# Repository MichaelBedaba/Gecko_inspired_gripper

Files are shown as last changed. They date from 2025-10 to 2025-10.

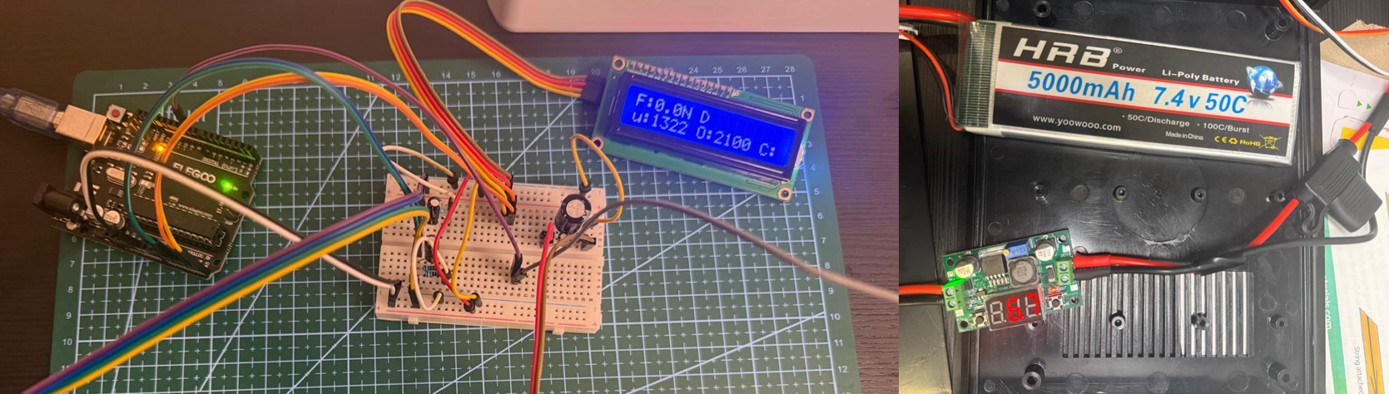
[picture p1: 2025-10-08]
Control Cicuit/setup.png

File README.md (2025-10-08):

# Development and Experimental Evaluation of Gecko-Inspired Robotic Gripper

## Code Procedures
1) **Force_Sensors_Calibration** → To calibrate FSRs with known weights; update M/B in code.
2) **Setting_Servo_Limits** → To set safe OPEN/CLOSE pulses (e.g., 2100/1500 μs) and save to EEPROM.
3) **Gripper_Operation_Testing** → To run integrated test: grip, read forces, show on LCD, log results.

## Required Libraries
- LiquidCrystal_I2C, Wire, EEPROM

## Wiring (Arduino Uno)
- Servo PWM → D9 (servo power from external 6 V, common GND)
- FSR Left → A0 (voltage divider 4.7k-ohm)
- FSR Right → A1 (voltage divider 4.7k-ohm)
- LCD SDA → A4, LCD SCL → A5

## Procedure

 **Power On:**
     -	Servo remains detached (no movement on startup).
     -	Arduino loads previous calibration and servo limit values from EEPROM.
 **Load Configuration:**
     -	Retrieve FSR calibration constants (M, B) and servo endpoint limits (OPEN/CLOSE µs).
 **Sensor Reading:**
     -	Continuously read force from Left (A0) and Right (A1) FSRs.
     -	Convert analog readings to Force (N) using calibration data.
     -	If total force exceeds predefined maximum → block servo closing.
 **Servo Activation (ARM):**
     -	Attach servo to enable motion.
     -	Manually adjust servo pulse width to control jaw opening/clamping.
     -	LCD displays real-time values:
             o	Total Force (N)
             o	Current servo pulse (µs)
             o	System status (ARM / DISARM)
 **Data Recording:**
     -	Record readings for each test object and jaw type.
     -	Include parameters such as object ID, pulse (µs), forces (N), slip, and surface marks.
 **Iteration:**
     -	Replace current jaw type (Gecko / Soft / Hard).
     -	Repeat measurement and recording for each configuration.
     -	Compare performance results across jaw types.

## By:
     Michael George - M00979224
     Supervisor: Dr. Judhi Prasetyo
     MSc Robotics, Middlesex University Dubai

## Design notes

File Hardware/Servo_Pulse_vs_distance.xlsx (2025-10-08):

Pulse (μs) | Jaw Distance
544 | 18.5
600 | 21
900 | 41
1200 | 60
1500 | 79.5
1800 | 98
2100 | 116

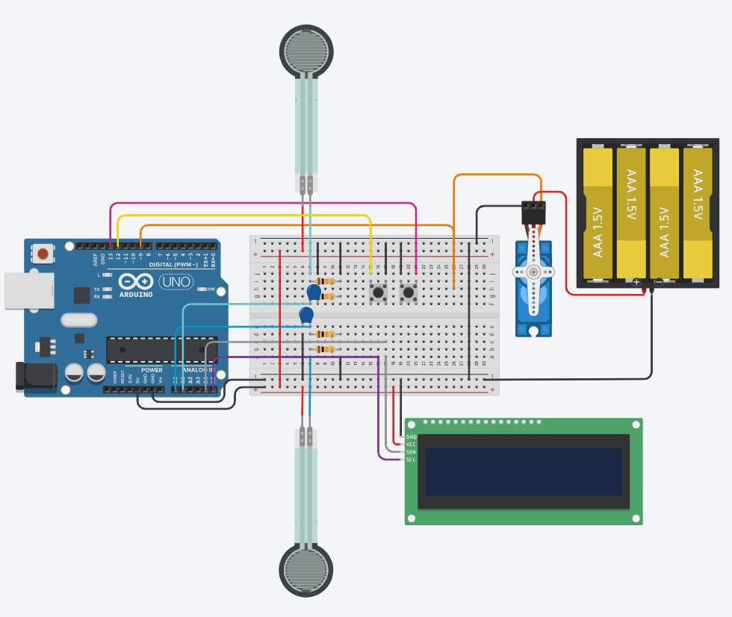
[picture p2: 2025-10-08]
Control Cicuit/Circuit_simplified.png

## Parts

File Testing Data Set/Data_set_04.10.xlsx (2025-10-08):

 | Object | Dimensions (width - mm) | Weight (kg) | Shape | Surface | material | Jaw Type / Pad | Jaw openning (μs) | Total Force (N) | Comments (slip, marks, etc.)
1 | Snow globe | 100 | 1 | Spherical | very smooth | Glass (Hard) | Gecko-material | 1750 | 3.9
2 | Water bottle | 88 | 1.5 | cylindrical | corrigated | PET - flexible | Gecko-material | 1500 | 7.4
3 | Teddy bear | 91 | 0.15 | irregular | soft fibers | polyester fiber - soft | Gecko-material | 1500 | 1.7
4 | ceramic cup | 71 | 0.2 | cylindrical | smooth | ceramic | Gecko-material | 1350 | 0.1
5 | raw eg | 42 | 0.08 | oval | fragile | raw | Gecko-material | 900 | 0.1
6 | apple | 74.5 | 0.2 | irregular | average - hardness | average - hardness | Gecko-material | 1400 | 2.3
7 | soft tomato | 56 | 0.12 | Spherical | smooth | very soft | Gecko-material | 1100 | 0.1
8 | paper cup | 67.5 | 0.2 | conic | fragile | paper | Gecko-material | 1150 | 1.6
 | Object | Dimensions (width - mm) | Weight (kg) | Shape | Surface | material | Jaw Type / Pad | Jaw openning (μs) | Total Force (N) | Comments (slip, marks, etc.)
1 | Snow globe | 100 | 1 | Spherical | very smooth | Glass (Hard) | Soft TPU | 1600 | 10.5 | slipped
2 | Water bottle | 88 | 1.5 | cylindrical | corrigated | PET - flexible | Soft TPU | 1200 | 14 | slipped
3 | Teddy bear | 91 | 0.15 | irregular | soft fibers | polyester fiber - soft | Soft TPU | 1400 | 3.4
4 | ceramic cup | 71 | 0.2 | cylindrical | smooth | ceramic | Soft TPU | 1300 | 5
5 | raw eg | 42 | 0.08 | oval | fragile | raw | Soft TPU | 850 | 1.9
6 | apple | 74.5 | 0.2 | irregular | average - hardness | average - hardness | Soft TPU | 1350 | 8.1
7 | soft tomato | 56 | 0.12 | Spherical | smooth | very soft | Soft TPU | 950 | 3.7 | minor compression
8 | paper cup | 67.5 | 0.2 | conic | fragile | paper | Soft TPU | 1100 | 0.7 | minor compression
 | Object | Dimensions (width - mm) | Weight (kg) | Shape | Surface | material | Jaw Type / Pad | Jaw openning (μs) | Total Force (N) | Comments (slip, marks, etc.)
1 | Snow globe | 100 | 1 | Spherical | very smooth | Glass (Hard) | hard TPU | 1500 | 16.2
2 | Water bottle | 88 | 1.5 | cylindrical | corrigated | PET - flexible | hard TPU |  |  | squeezed the bottle - failed to lift
3 | Teddy bear | 91 | 0.15 | irregular | soft fibers | polyester fiber - soft | hard TPU | 1350 | 5.9
4 | ceramic cup | 71 | 0.2 | cylindrical | smooth | ceramic | hard TPU | 1300 | 7.2
5 | raw eg | 42 | 0.08 | oval | fragile | raw | hard TPU |  |  | didn't catch - stopped to avoid crashing
6 | apple | 74.5 | 0.2 | irregular | average - hardness | average - hardness | hard TPU | 1350 | 10.7
7 | soft tomato | 56 | 0.12 | Spherical | smooth | very soft | hard TPU | 950 | 6.3
8 | paper cup | 67.5 | 0.2 | conic | fragile | paper | hard TPU | 1100 | 3

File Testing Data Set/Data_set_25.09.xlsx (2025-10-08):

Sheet: 25.09
 | Object | Dimensions (width - mm) | Weight (kg) | Shape | Surface | material | Jaw Type / Pad | Total Force (N) | Comments (slip, marks, etc.)
1 | Snow globe | 100 | 1 | Spherical | very smooth | Glass (Hard) | Gecko-material | 28
2 | Water bottle | 88 | 1.5 | cylindrical | corrigated | PET - flexible | Gecko-material | 21 N
3 | Teddy bear | 91 | 0.15 | irregular | soft fibers | polyester fiber - soft | Gecko-material | 0.2
4 | ceramic cup | 71 | 0.2 | cylindrical | smooth | ceramic | Gecko-material | 1.6
5 | raw eg | 42 | 0.08 | oval | fragile | raw | Gecko-material | 1
6 | apple | 74.5 | 0.2 | irregular | average - hardness | average - hardness | Gecko-material | 2.7
7 | soft tomato | 56 | 0.12 | Spherical | smooth | very soft | Gecko-material | 0.1
8 | paper cup | 67.5 | 0.2 | conic | fragile | paper | Gecko-material | 2.1
1 | Snow globe | 100 | 1 | Spherical | very smooth | Glass (Hard) | Soft TPU | 18
2 | Water bottle | 88 | 1.5 | cylindrical | corrigated | PET - flexible | Soft TPU | 15
3 | Teddy bear | 91 | 0.15 | irregular | soft fibers | polyester fiber - soft | Soft TPU | 2
4 | ceramic cup | 71 | 0.2 | cylindrical | smooth | ceramic | Soft TPU | 10.2
5 | raw eg | 42 | 0.08 | oval | fragile | raw | Soft TPU | 1.8
6 | apple | 74.5 | 0.2 | irregular | average - hardness | average - hardness | Soft TPU | 6
7 | soft tomato | 56 | 0.12 | Spherical | smooth | very soft | Soft TPU | 2.2 | minor compression
8 | paper cup | 67.5 | 0.2 | conic | fragile | paper | Soft TPU | 2.5
1 | Snow globe | 100 | 1 | Spherical | very smooth | Glass (Hard) | hard TPU | 26
2 | Water bottle | 88 | 1.5 | cylindrical | corrigated | PET - flexible | hard TPU | 30.2 | squeezed the bottle - failed to lift
3 | Teddy bear | 91 | 0.15 | irregular | soft fibers | polyester fiber - soft | hard TPU | 1
4 | ceramic cup | 71 | 0.2 | cylindrical | smooth | ceramic | hard TPU | 12
5 | raw eg | 42 | 0.08 | oval | fragile | raw | hard TPU | NA | didn't catch - stopped to avoid crashing
6 | apple | 74.5 | 0.2 | irregular | average - hardness | average - hardness | hard TPU | 16.5
7 | soft tomato | 56 | 0.12 | Spherical | smooth | very soft | hard TPU | 3
8 | paper cup | 67.5 | 0.2 | conic | fragile | paper | hard TPU | 2.8

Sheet: Combined
Object | Dim (mm) | Wt (kg) | Shape | Surface | Material (Object) | Gecko-material Force (N) | Soft TPU Force (N) | Hard TPU Force (N)
Snow globe | 100 | 1 | Spherical | Very smooth | Glass (hard) | 28 | 18 | 26
Water bottle | 88 | 1.5 | Cylindrical | Corrugated | PET (flexible) | 21 | 15 | 30.2
Teddy bear | 91 | 0.15 | Irregular | Soft fibers | Polyester fiber | 0.2 | 2 | 1
Ceramic cup | 71 | 0.2 | Cylindrical | Smooth | Ceramic | 1.6 | 10.2 | 12
Raw egg | 42 | 0.08 | Oval | Fragile | Egg shell | 1 | 1.8 | NA
Apple | 74.5 | 0.2 | Irregular | Medium-hard | Organic tissue | 2.7 | 6 | 16.5
Soft tomato | 56 | 0.12 | Spherical | Smooth/soft | Organic tissue | 0.1 | 2.2 | 3
Paper cup | 67.5 | 0.2 | Conic | Fragile | Paper | 2.1 | 2.5 | 2.8
Object | Gecko Comments |  |  | Soft TPU Comments |  |  | Hard TPU Comments
Snow globe | Strong adhesion, risk of slip on curve |  |  | Stable, cushioned grip |  |  | Firm hold, risk of slip marks
Water bottle | needed partial squeeze to hold - surface increase |  |  | slight squeeze - slipping risk |  |  | Squeezed, failed to lift
Teddy bear | Adhesion ineffective |  |  | Gentle, best option |  |  | Poor grip, risk of damage
Ceramic cup | stable adhesion |  |  | Good grip, cushioned |  |  | Strong grip, may scratch
Raw egg | Gentle hold |  |  | cushioned - crushing risk |  |  | Stopped (too risky)
Apple | strong adhesion |  |  | Balanced, good control |  |  | Very strong, risk of bruising
Soft tomato | Gentle hold |  |  | partial squeeze |  |  | surface damage
Paper cup | Adhesion after partial squeeze - conic shape |  |  | partial squeeze - not stable |  |  | deformed

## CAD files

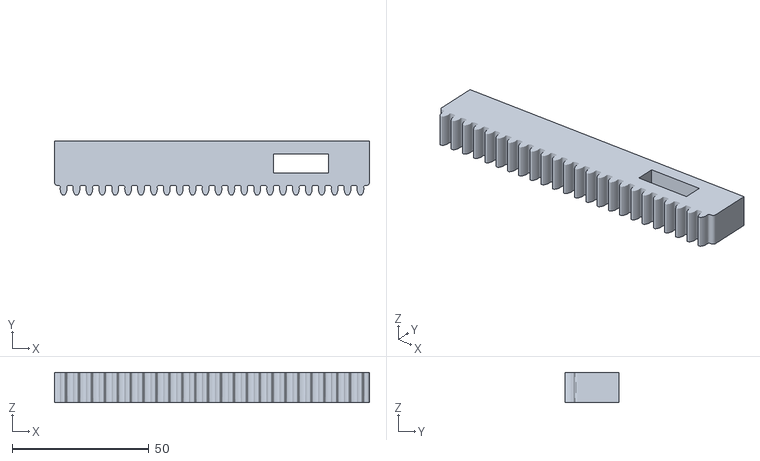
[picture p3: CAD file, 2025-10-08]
Hardware/3D_STL_Fusion_Printing/4_Rack_x2.stl
115.0 x 19.8 x 11.0

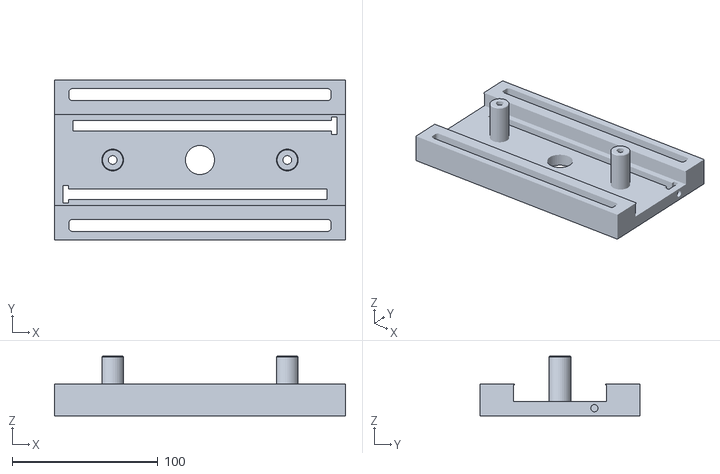
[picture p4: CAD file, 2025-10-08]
Hardware/3D_STL_Fusion_Printing/3_Racks_guide_frame.stl
200.0 x 110.0 x 41.0

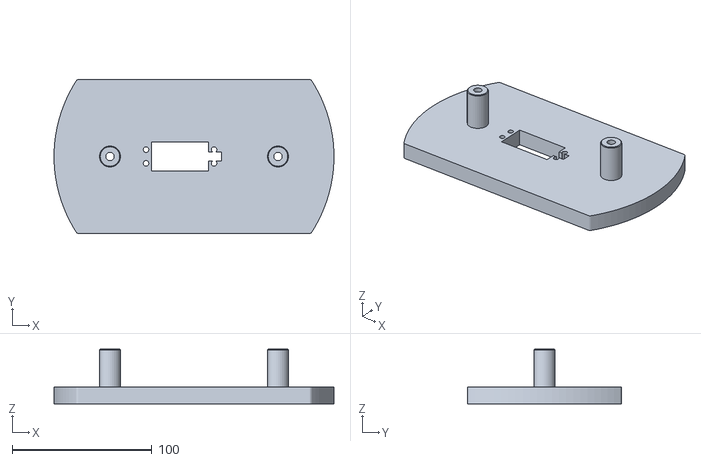
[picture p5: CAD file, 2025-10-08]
Hardware/3D_STL_Fusion_Printing/2_Motor_base_1.stl
200.0 x 110.0 x 39.0

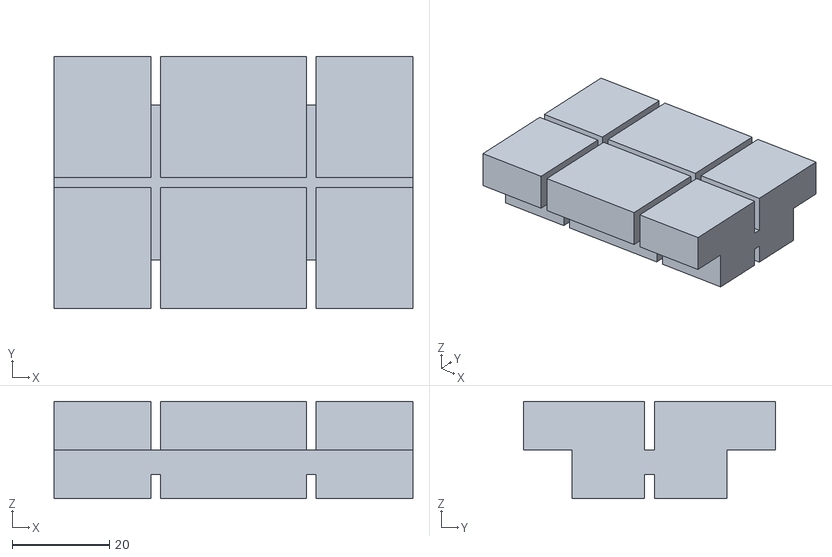
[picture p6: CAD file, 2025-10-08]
Hardware/3D_STL_Fusion_Printing/8_jaw_rubber_x6.stl
74.0 x 52.0 x 20.0

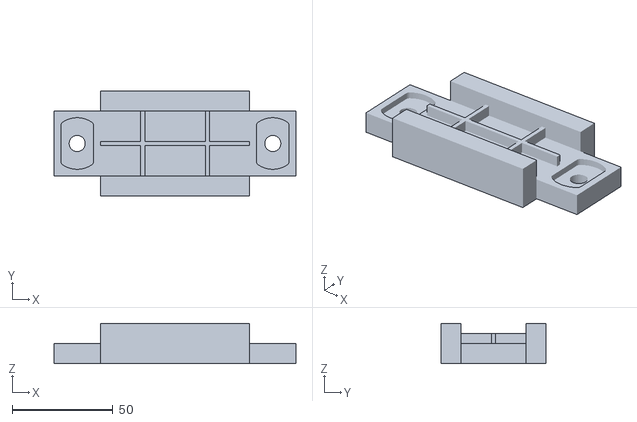
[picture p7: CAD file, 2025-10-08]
Hardware/3D_STL_Fusion_Printing/7_Jaw_module_x6.stl
120.0 x 52.0 x 20.0

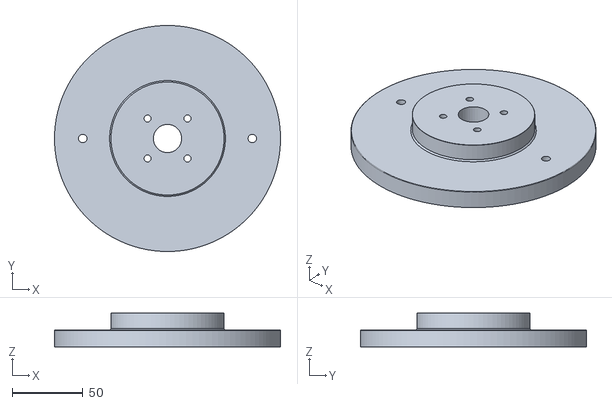
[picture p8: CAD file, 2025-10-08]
Hardware/3D_STL_Fusion_Printing/1_Arm_flange.stl
160.0 x 160.0 x 24.0

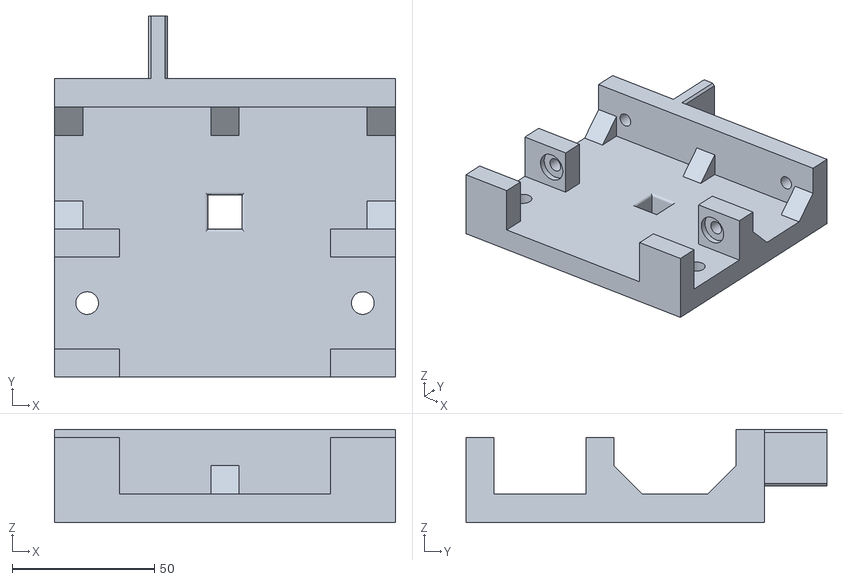
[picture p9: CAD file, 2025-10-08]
Hardware/3D_STL_Fusion_Printing/6_Gripper_Jaw_x2.stl
120.0 x 127.0 x 32.7

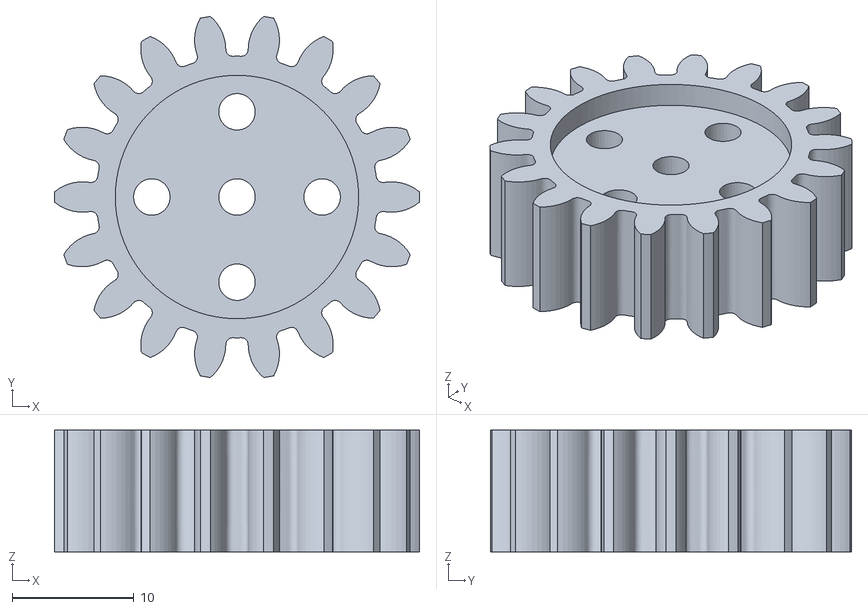
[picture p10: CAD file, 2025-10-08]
Hardware/3D_STL_Fusion_Printing/5_Pinion.stl
30.0 x 29.7 x 10.0

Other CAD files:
Hardware/2D_CAD_Drawings/0_Main_Gripper-rack-and-pinion.dwg
Hardware/2D_CAD_Drawings/Motor_base_1.dwg
Hardware/2D_CAD_Drawings/racks_guide_frame.dwg
Hardware/2D_CAD_Drawings/Arm_flange.dwg
Hardware/2D_CAD_Drawings/Pinion_Rack.dwg
Hardware/2D_CAD_Drawings/Gripper_Jaw.dwg
Hardware/2D_CAD_Drawings/jaw_module.dwg

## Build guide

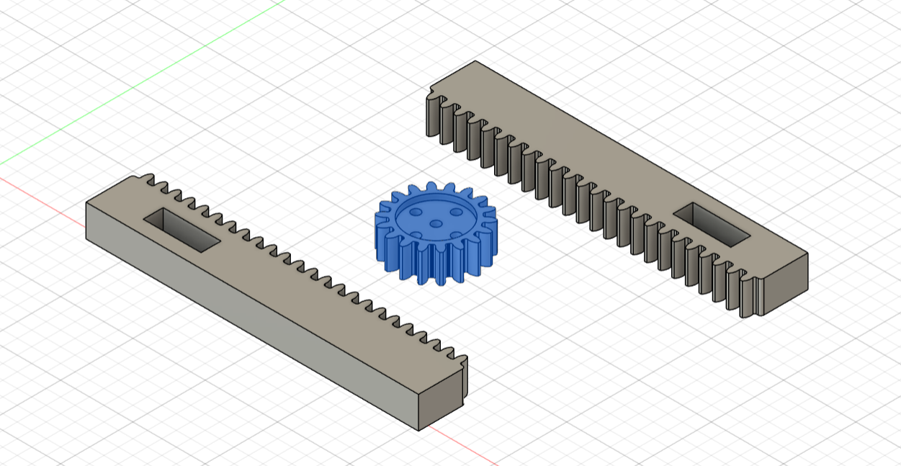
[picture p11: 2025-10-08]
Hardware/3D_STL_Fusion_Printing/Pinion_racks.png

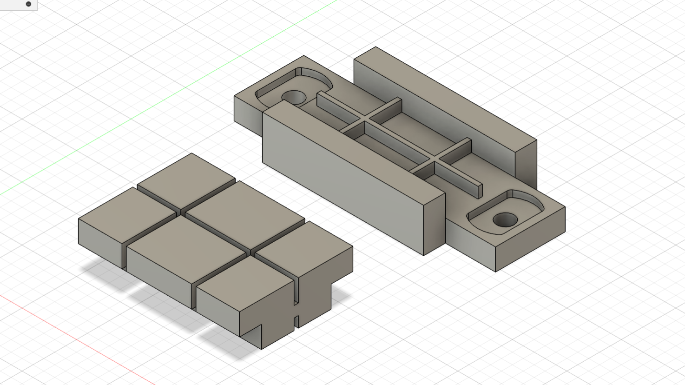
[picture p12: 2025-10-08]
Hardware/3D_STL_Fusion_Printing/Jaw_module.png

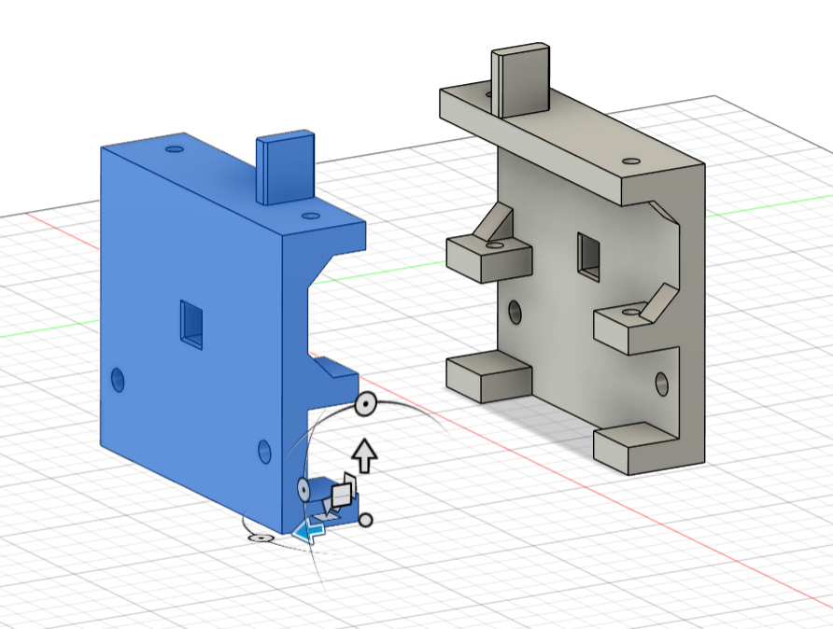
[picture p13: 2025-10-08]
Hardware/3D_STL_Fusion_Printing/Jaws.png

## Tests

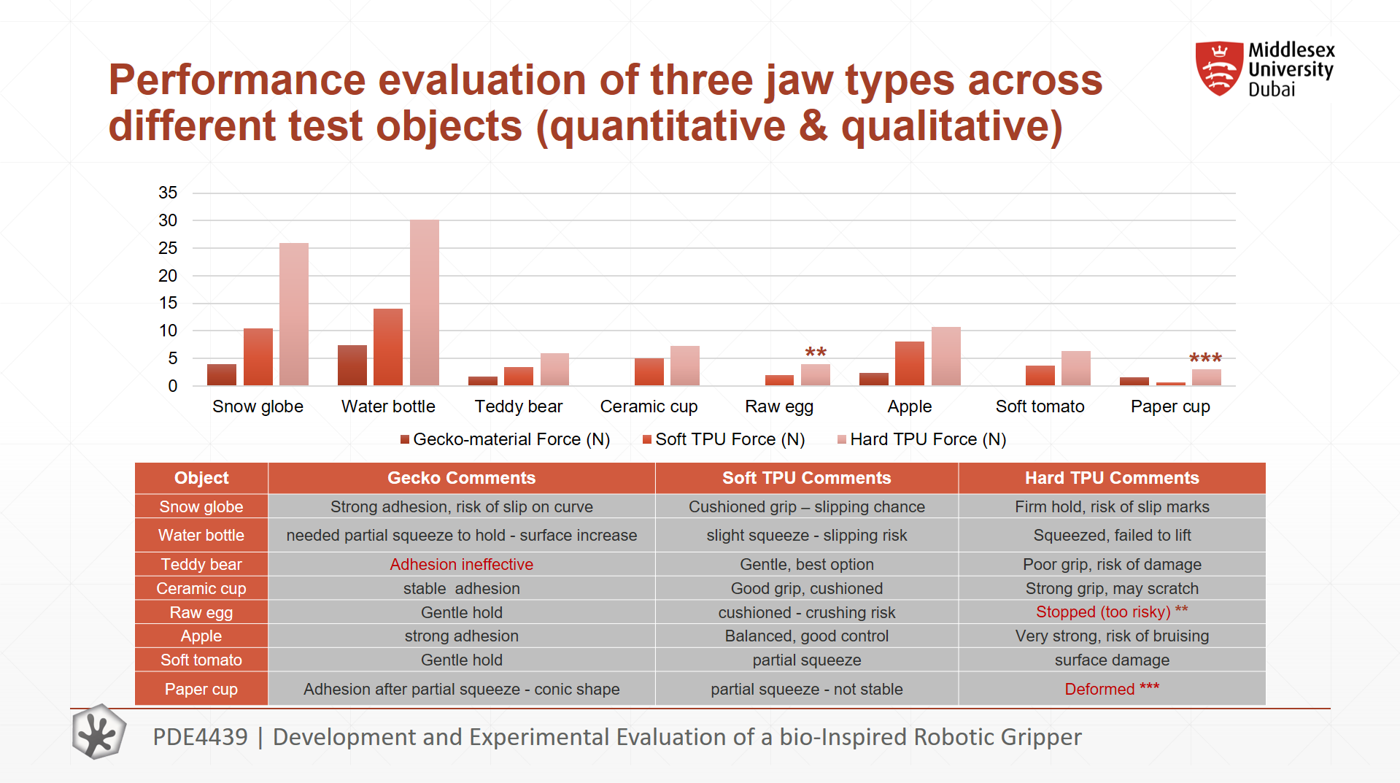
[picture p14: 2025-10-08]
Testing Data Set/Performance_evaluation.png

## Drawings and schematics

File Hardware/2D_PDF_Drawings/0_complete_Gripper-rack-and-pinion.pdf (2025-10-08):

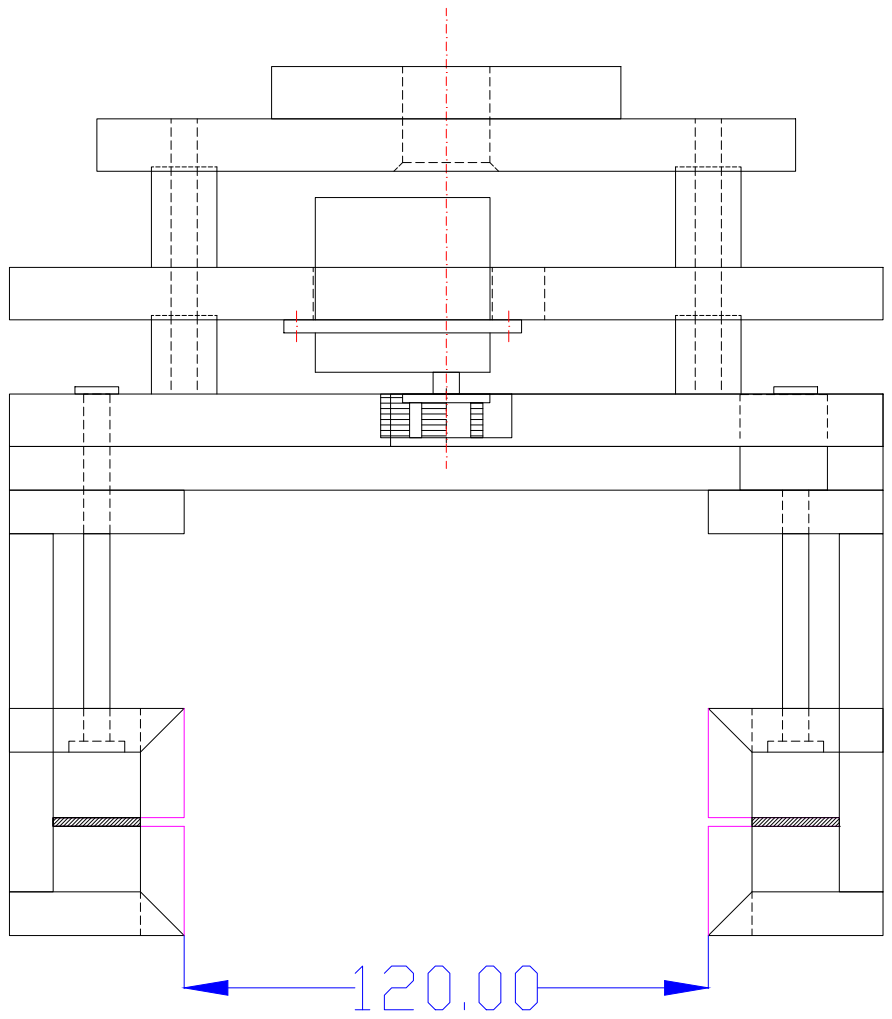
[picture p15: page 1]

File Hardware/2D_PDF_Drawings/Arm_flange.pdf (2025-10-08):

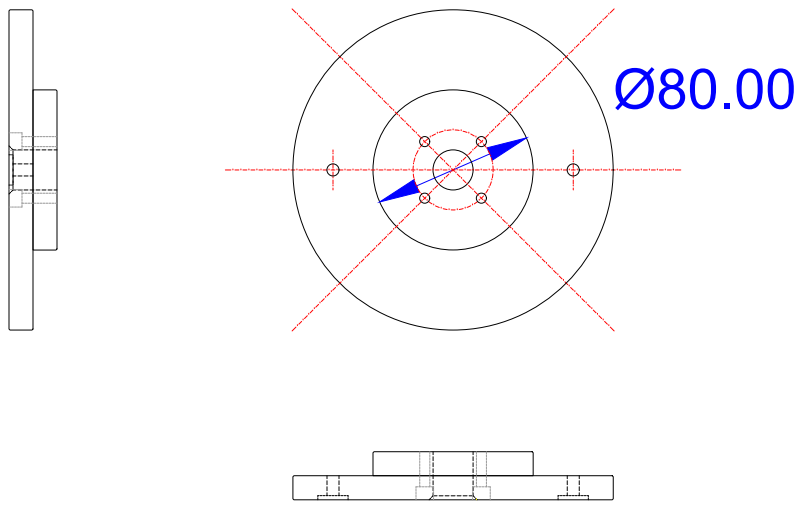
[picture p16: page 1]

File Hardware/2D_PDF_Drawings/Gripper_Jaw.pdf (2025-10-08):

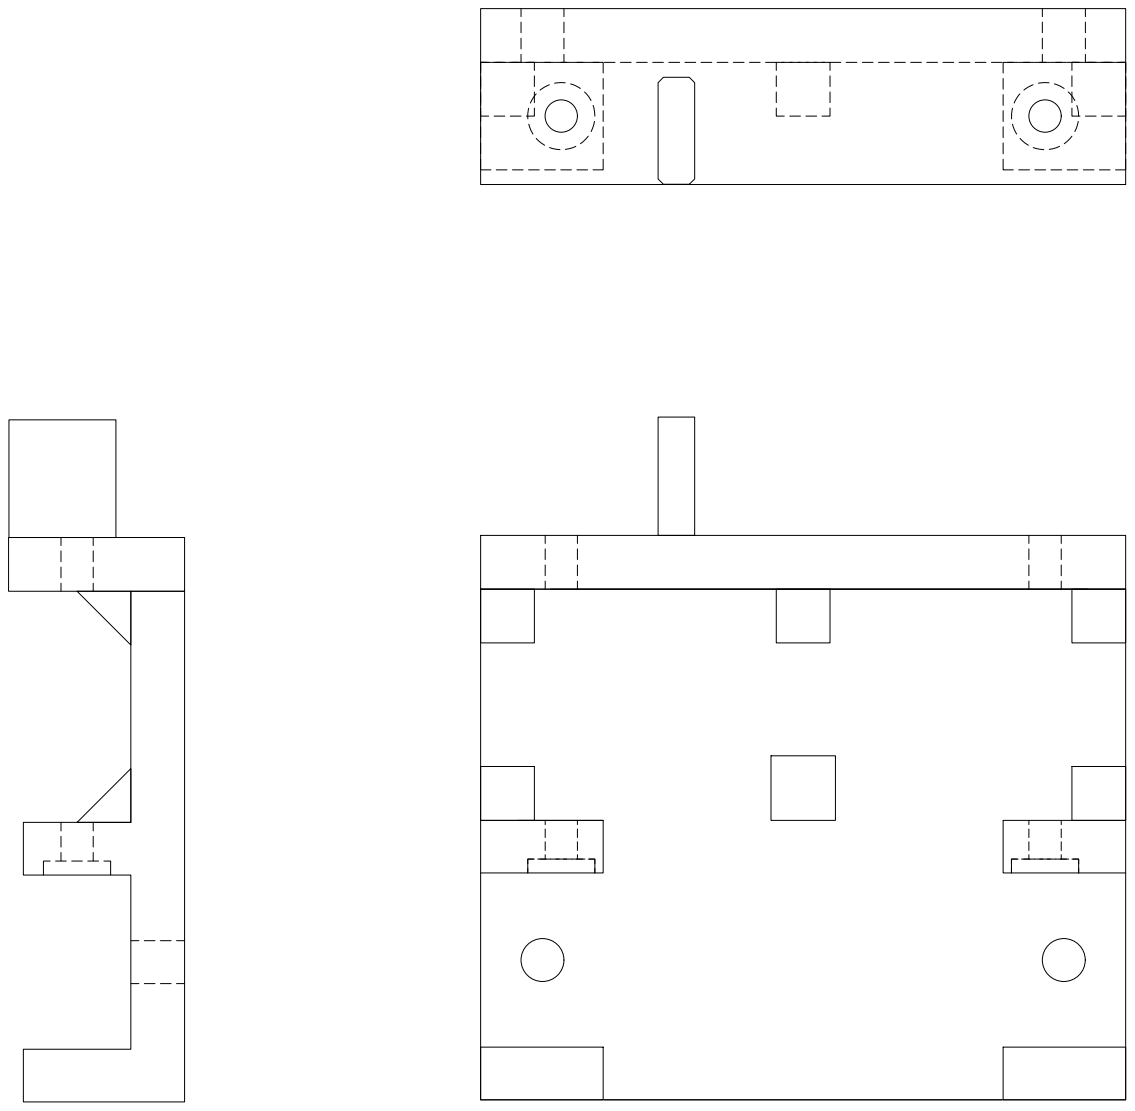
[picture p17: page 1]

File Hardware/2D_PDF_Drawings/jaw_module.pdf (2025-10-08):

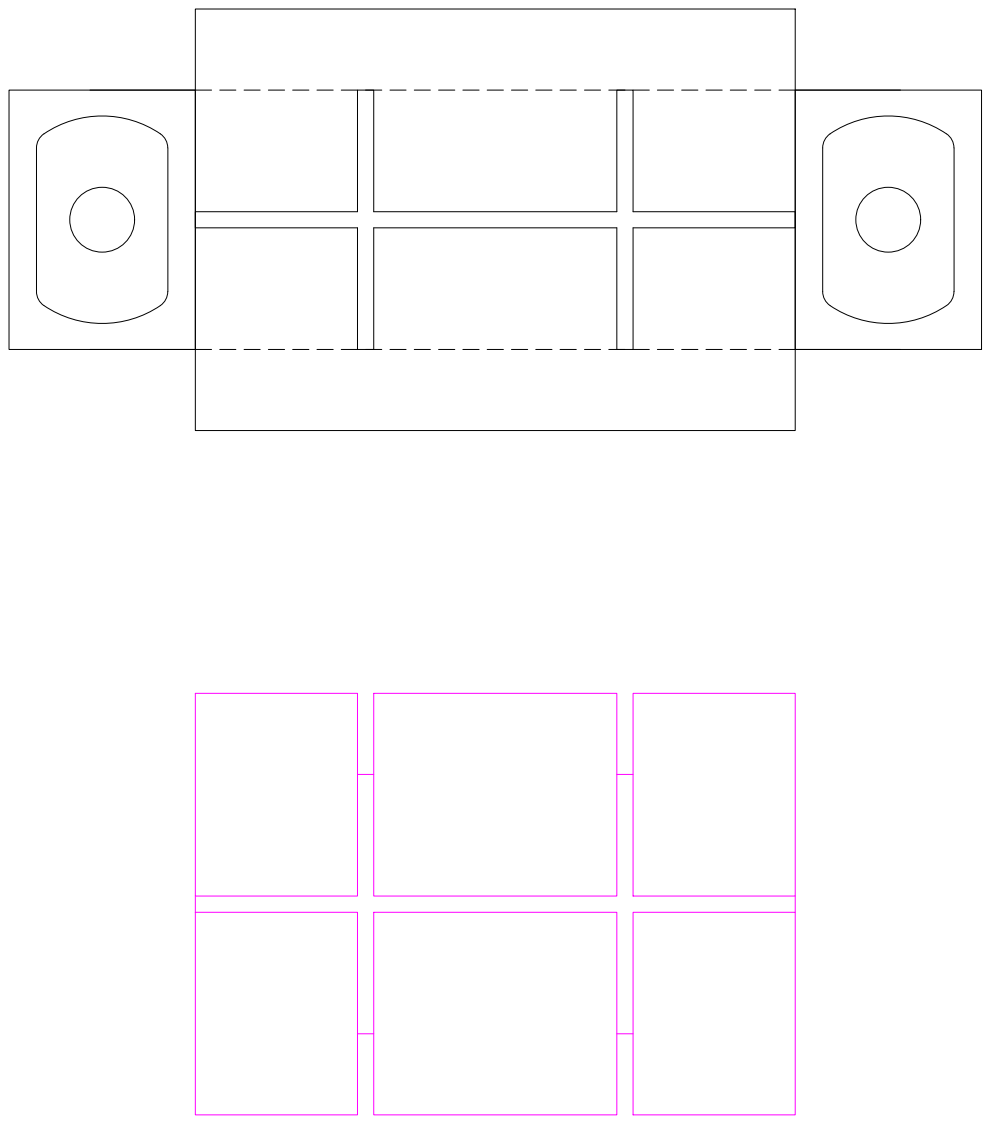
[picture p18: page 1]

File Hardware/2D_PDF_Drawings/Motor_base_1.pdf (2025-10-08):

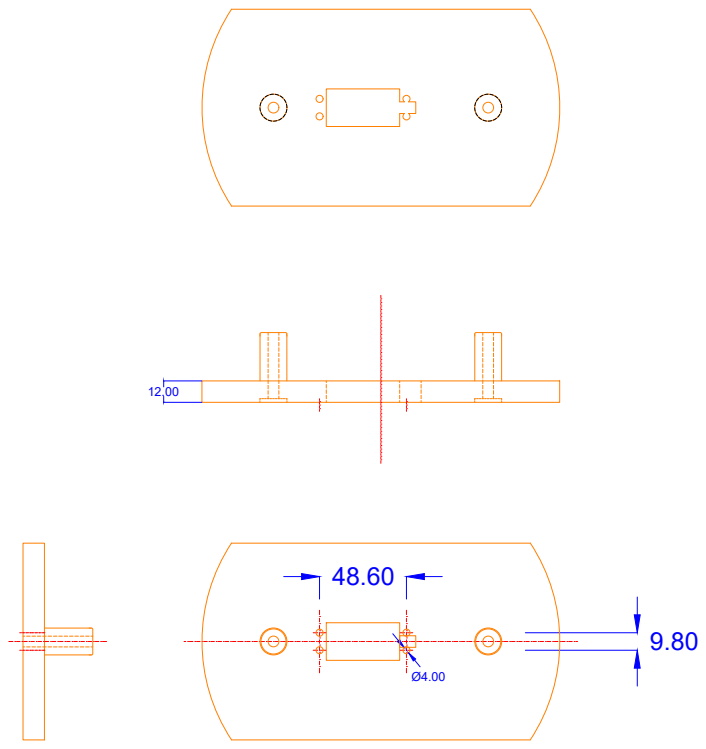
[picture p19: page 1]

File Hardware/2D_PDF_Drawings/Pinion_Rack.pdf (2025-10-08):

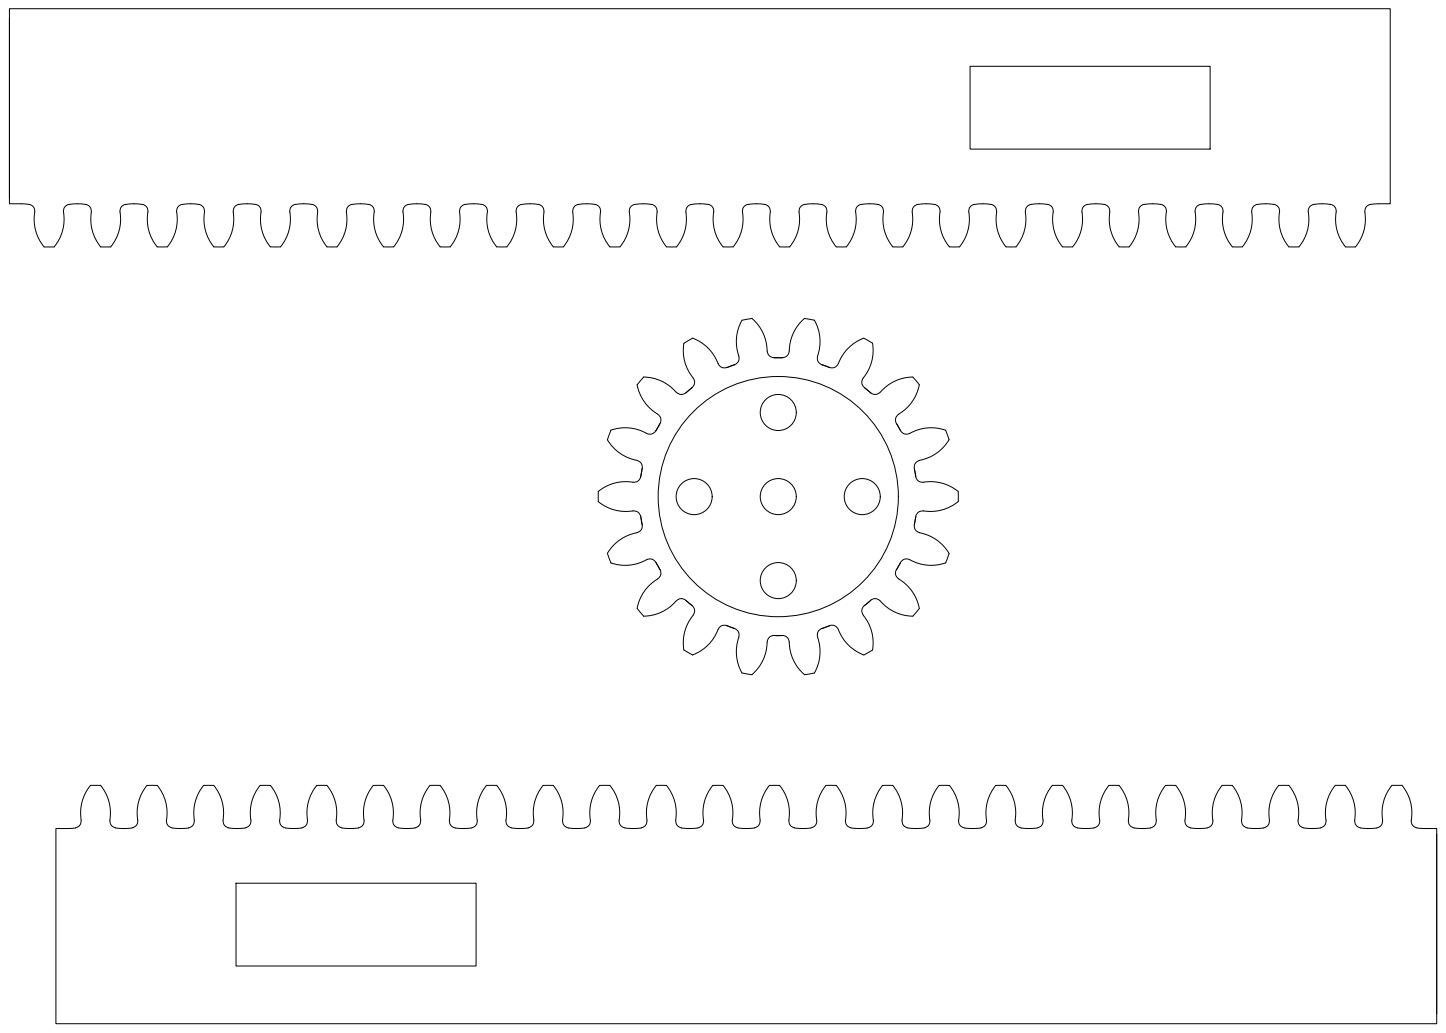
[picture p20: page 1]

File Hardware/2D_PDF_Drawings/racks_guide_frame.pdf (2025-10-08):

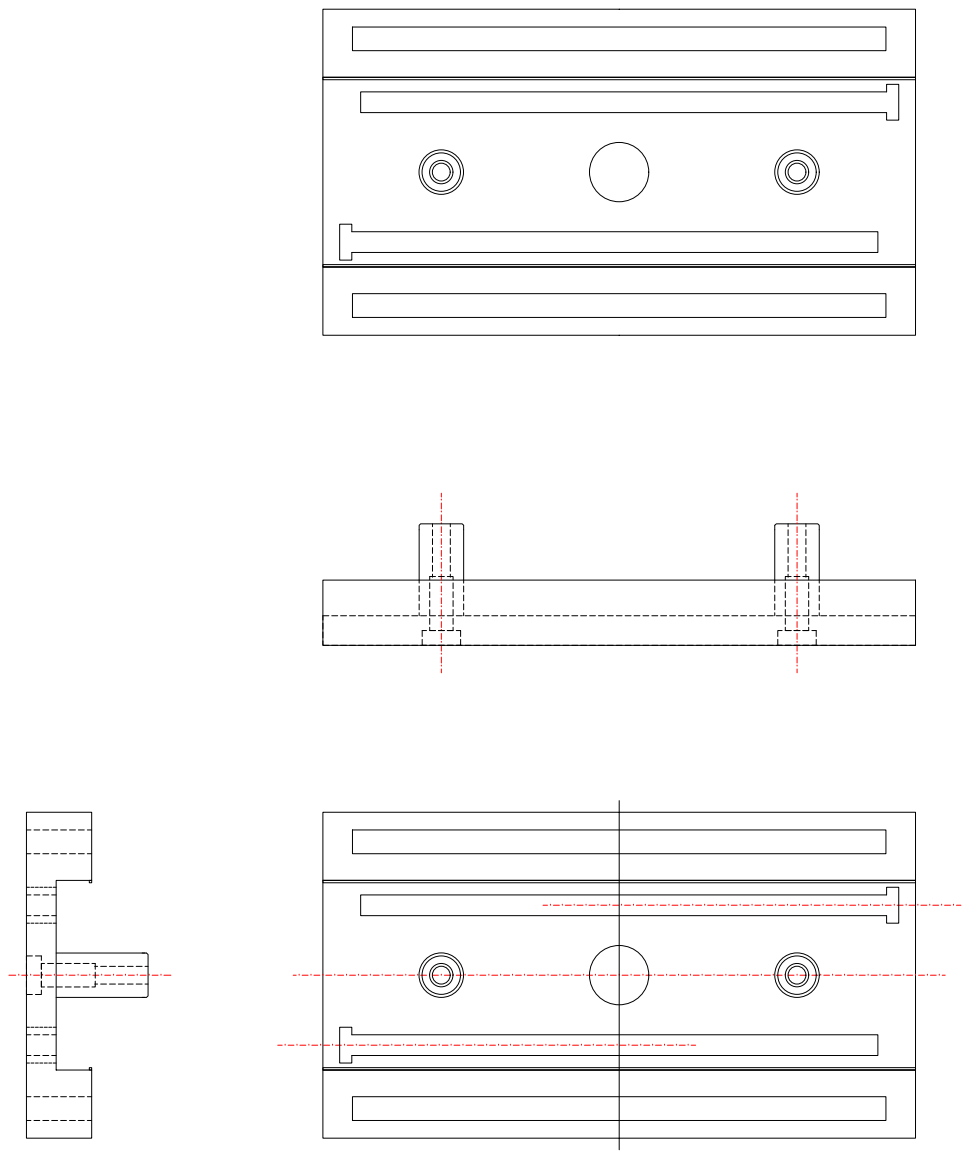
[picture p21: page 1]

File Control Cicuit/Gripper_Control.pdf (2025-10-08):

A

1 | 2 | 3 | 4 | 5 | 6

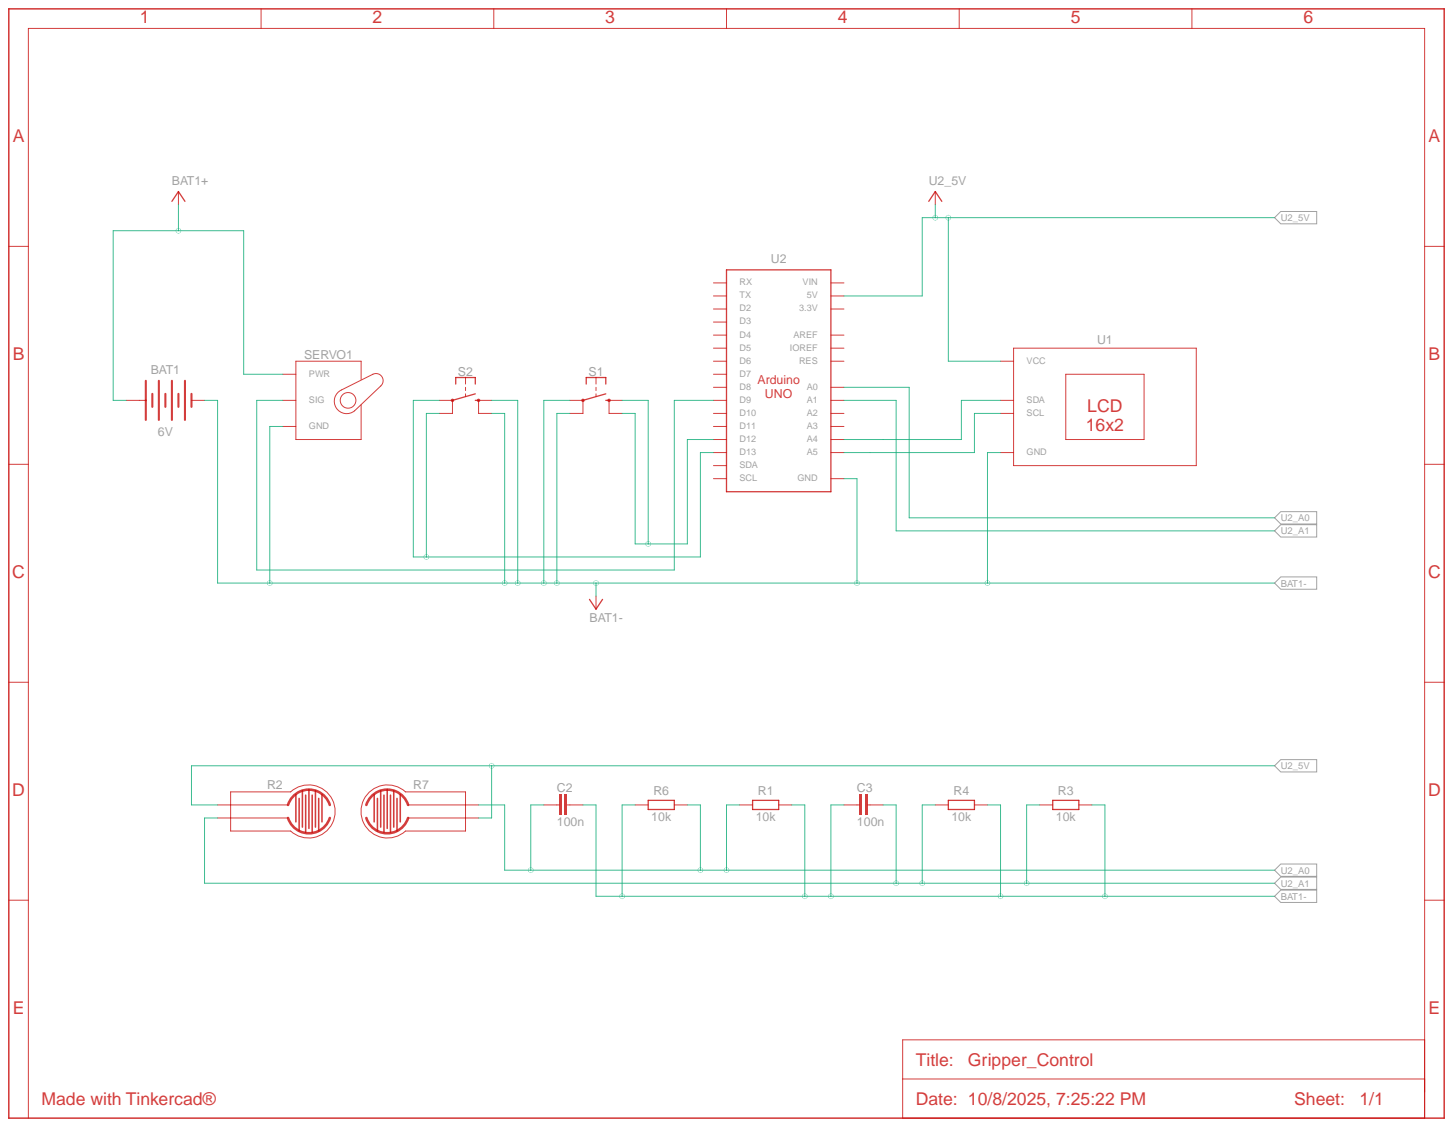
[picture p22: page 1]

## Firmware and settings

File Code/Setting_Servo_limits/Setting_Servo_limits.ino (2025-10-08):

#include <Servo.h>
#include <EEPROM.h>

Servo s;
const int SERVO_PIN = 9;

struct EP {
  uint32_t magic;
  int usOpen;
  int usClose;
};
const uint32_t EP_MAGIC = 0x454E444Fu;
const int EP_ADDR = 128;

EP ep;

bool armed = false;
int curUs = 1500;
int msPerStep = 6;
const int FINE = 2;
const int COARSE = 10;

void loadEP(){
  EEPROM.get(EP_ADDR, ep);
  if (ep.magic != EP_MAGIC) { ep.magic = EP_MAGIC; ep.usOpen = 1500; ep.usClose = 1500; }
}
void saveEP(){ ep.magic = EP_MAGIC; EEPROM.put(EP_ADDR, ep); }

void printEP(const char* tag=nullptr){
  if(tag){ Serial.print(tag); Serial.print(" "); }
  Serial.print(F("curUs=")); Serial.print(curUs);
  Serial.print(F("  OPEN(us)=")); Serial.print(ep.usOpen);
  Serial.print(F("  CLOSE(us)=")); Serial.println(ep.usClose);
}

void rampTo(int target){
  target = constrain(target, 500, 2500);
  int step = (target > curUs) ? +1 : -1;
  while (curUs != target){
    curUs += step;
    if (armed) { s.writeMicroseconds(curUs); delay(msPerStep); }
    else delay(1);
  }
}

void armNow(){
  if (armed) return;
  s.attach(SERVO_PIN);
  s.writeMicroseconds(curUs);
  armed = true;
  printEP("[ARMED]");
}

void disarmNow(){
  if (!armed) return;
  s.detach();
  armed = false;
  Serial.println(F("[DISARMED]"));
}

void setup(){
  Serial.begin(9600);
  loadEP();
  curUs = (ep.usOpen + ep.usClose) / 2;
  printEP("[BOOT]");
}

void loop(){
  if (Serial.available()){
    char c = Serial.read();

    if (c=='a' || c=='A') armNow();
    if (c=='x' || c=='X') disarmNow();

    if (c=='[') rampTo(curUs - FINE);
    if (c==']') rampTo(curUs + FINE);
    if (c=='-') rampTo(curUs - COARSE);
    if (c=='+') rampTo(curUs + COARSE);

    if (c=='u' || c=='U'){ int v = Serial.parseInt(); if (v>0) rampTo(v); printEP("[u]"); }

    if (c=='o' || c=='O'){ if (c=='O') { ep.usOpen = curUs; printEP("[SET OPEN]"); }
                           else if (armed) rampTo(ep.usOpen); }
    if (c=='c' || c=='C'){ if (c=='C') { ep.usClose = curUs; printEP("[SET CLOSE]"); }
                           else if (armed) rampTo(ep.usClose); }

    if (c=='S'){ saveEP(); Serial.println(F("[SAVED]")); }
    if (c=='p' || c=='P') printEP("[p]");
  }
}

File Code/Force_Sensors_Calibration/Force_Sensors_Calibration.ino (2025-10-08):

#include <Wire.h>
#include <LiquidCrystal_I2C.h>
#include <EEPROM.h>
#include <math.h>

#define LCD_ADDR 0x27
LiquidCrystal_I2C lcd(LCD_ADDR, 16, 2);

const int PIN_L = A0;
const int PIN_R = A1;

struct CalData {
  uint32_t magic;
  float M_L, B_L;
  float M_R, B_R;
  float tot_gain;
};
const uint32_t CAL_MAGIC = 0xA17F5F5Ful;
const int EEPROM_ADDR = 0;

CalData cal = {CAL_MAGIC, 182.0f, 353.7f, 124.0f, 371.3f, 1.0f};

const int N_AVG = 10;
int bufL[N_AVG] = {0}, bufR[N_AVG] = {0};
int idxAvg = 0, filled = 0, sumL = 0, sumR = 0;

float tareL = 0.0f, tareR = 0.0f;
unsigned long lastLcd = 0;

int readADCavg(int pin) {
  long acc = 0;
  for (int i = 0; i < 20; i++) { acc += analogRead(pin); delay(2); }
  return (int)(acc / 20);
}
void lcdClearLine(uint8_t row){
  lcd.setCursor(0,row); lcd.print("                ");
}
void lcdTop(const String &s) { lcdClearLine(0); lcd.setCursor(0,0); lcd.print(s); }
void lcdBot(const String &s) { lcdClearLine(1); lcd.setCursor(0,1); lcd.print(s); }

void loadCal() {
  CalData tmp;
  EEPROM.get(EEPROM_ADDR, tmp);
  if (tmp.magic == CAL_MAGIC && isfinite(tmp.M_L) && isfinite(tmp.M_R)) {
    cal = tmp;
    if (!(cal.tot_gain > 0.2f && cal.tot_gain < 5.0f)) cal.tot_gain = 1.0f;
  }
}
void saveCal() { EEPROM.put(EEPROM_ADDR, cal); }

void tareNow() {
  int aL = readADCavg(PIN_L);
  int aR = readADCavg(PIN_R);
  float kgL = (aL - cal.B_L) / cal.M_L;
  float kgR = (aR - cal.B_R) / cal.M_R;
  tareL = kgL; tareR = kgR;
}

void fitLineLR(const float *x, const int *yL, const int *yR, int n,
               float &ML, float &BL, float &MR, float &BR) {
  double Sx = 0, Sx2 = 0, SyL = 0, SyR = 0, SxSyL = 0, SxSyR = 0;
  for (int i = 0; i < n; i++) {
    double xi = x[i];
    Sx += xi; Sx2 += xi * xi;
    SyL += yL[i]; SyR += yR[i];
    SxSyL += xi * yL[i]; SxSyR += xi * yR[i];
  }
  double denom = (n * Sx2 - Sx * Sx);
  if (denom == 0) denom = 1;
  ML = (float)((n * SxSyL - Sx * SyL) / denom);
  BL = (float)((SyL - ML * Sx) / n);
  MR = (float)((n * SxSyR - Sx * SyR) / denom);
  BR = (float)((SyR - MR * Sx) / n);
}

void runCalibration() {
  const int NPTS = 3;
  float W[NPTS] = {0.5f, 1.0f, 1.5f};
  int YL[NPTS], YR[NPTS];

  lcdTop("CAL: place 0.5kg"); lcdBot("Press '1' to cap");
  Serial.println(F("[CAL] Place 0.5 kg, press '1' to capture"));
  while (true) { if (Serial.available() && Serial.read() == '1') { YL[0] = readADCavg(PIN_L); YR[0] = readADCavg(PIN_R); break; } }

  lcdTop("CAL: place 1.0kg"); lcdBot("Press '2' to cap");
  Serial.println(F("[CAL] Place 1.0 kg, press '2' to capture"));
  while (true) { if (Serial.available() && Serial.read() == '2') { YL[1] = readADCavg(PIN_L); YR[1] = readADCavg(PIN_R); break; } }

  lcdTop("CAL: place 1.5kg"); lcdBot("Press '3' to cap");
  Serial.println(F("[CAL] Place 1.5 kg, press '3' to capture"));
  while (true) { if (Serial.available() && Serial.read() == '3') { YL[2] = readADCavg(PIN_L); YR[2] = readADCavg(PIN_R); break; } }

  float ML, BL, MR, BR;
  fitLineLR(W, YL, YR, NPTS, ML, BL, MR, BR);

  cal.M_L = ML; cal.B_L = BL;
  cal.M_R = MR; cal.B_R = BR;
  cal.magic = CAL_MAGIC;
  saveCal();

  tareL = 0; tareR = 0;
  Serial.println(F("[CAL] Done. New params:"));
  Serial.print(F("  Left:  M=")); Serial.print(cal.M_L, 2); Serial.print(F("  B=")); Serial.println(cal.B_L, 2);
  Serial.print(F("  Right: M=")); Serial.print(cal.M_R, 2); Serial.print(F("  B=")); Serial.println(cal.B_R, 2);

  lcdTop("CAL saved ✓"); lcdBot("t=Zero  g/k=Gain");
  delay(1000);
}

void setup() {
  Serial.begin(9600);
  Serial.setTimeout(5000);

  Wire.begin();
  lcd.init();
  lcd.backlight();

  lcdTop("FSR Scale v1.3");
  lcdBot("Loading cal...");
  loadCal();
  delay(600);

  for (int i = 0; i < N_AVG; i++) {
    int rl = analogRead(PIN_L);
    int rr = analogRead(PIN_R);
    bufL[i] = rl; bufR[i] = rr; sumL += rl; sumR += rr;
    delay(5);
  }
  filled = N_AVG;

  lcdTop("t=Tare c=Cal");
  lcdBot("g/k=Gain, p=par");
  delay(700);
}

void loop() {
  int rl = analogRead(PIN_L);
  int rr = analogRead(PIN_R);
  sumL -= bufL[idxAvg]; sumR -= bufR[idxAvg];
  bufL[idxAvg] = rl;   bufR[idxAvg] = rr;
  sumL += bufL[idxAvg]; sumR += bufR[idxAvg];
  idxAvg = (idxAvg + 1) % N_AVG;

  float adcL = sumL / float(filled);
  float adcR = sumR / float(filled);

  float kgL = (adcL - cal.B_L) / cal.M_L - tareL; if (kgL < 0) kgL = 0;
  float kgR = (adcR - cal.B_R) / cal.M_R - tareR; if (kgR < 0) kgR = 0;

  float kgSum = kgL + kgR;
  float kgSumDisp = kgSum * cal.tot_gain;

  if (millis() - lastLcd > 250) {
    lastLcd = millis();

    lcdClearLine(0);
    lcd.setCursor(0,0);
    lcd.print("L:");   lcd.print(kgL, 2);
    lcd.print(" R:");  lcd.print(kgR, 2);

    lcdClearLine(1);
    lcd.setCursor(0,1);
    lcd.print("SUM:"); lcd.print(kgSumDisp, 2); lcd.print("kg");
  }

  if (Serial.available()) {
    char c = Serial.read();

    if (c == 't' || c == 'T') {
      tareNow();
      lcdTop("Tare set (0 kg)");
      delay(800);
    }

    if (c == 'c' || c == 'C') {
      while (Serial.available()) Serial.read();
      runCalibration();
    }

    if (c == 'p' || c == 'P') {
      Serial.println(F("[PARAMS]"));
      Serial.print(F("L: M=")); Serial.print(cal.M_L, 4); Serial.print(F("  B=")); Serial.println(cal.B_L, 2);
      Serial.print(F("R: M=")); Serial.print(cal.M_R, 4); Serial.print(F("  B=")); Serial.println(cal.B_R, 2);
      Serial.print(F("TOT_GAIN=")); Serial.println(cal.tot_gain, 4);
      lcdTop("Sent: params"); delay(600);
    }

    if (c == 'g' || c == 'G') {
      float L = (readADCavg(PIN_L) - cal.B_L) / cal.M_L - tareL; if (L < 0) L = 0;
      float R = (readADCavg(PIN_R) - cal.B_R) / cal.M_R - tareR; if (R < 0) R = 0;
      float sum = L + R;
      if (sum > 0.01f) {
        cal.tot_gain = 1.0f / sum;
        saveCal();
        lcdTop("Gain set: 1.00kg"); delay(1200);
      } else {
        lcdTop("Put weight first"); delay(1000);
      }
    }

    if (c == 'k' || c == 'K') {
      float ref = Serial.parseFloat();
      float L = (readADCavg(PIN_L) - cal.B_L) / cal.M_L - tareL; if (L < 0) L = 0;
      float R = (readADCavg(PIN_R) - cal.B_R) / cal.M_R - tareR; if (R < 0) R = 0;
      float sum = L + R;
      if (ref > 0.05f && sum > 0.01f) {
        cal.tot_gain = ref / sum;
        saveCal();
        lcdTop("Gain saved"); delay(1000);
      } else {
        lcdTop("Bad ref/sum"); delay(800);
      }
    }

    if (c == 'r' || c == 'R') {
      cal.tot_gain = 1.0f; saveCal();
      lcdTop("Gain reset (1x)"); delay(800);
    }

    if (c == 's' || c == 'S') {
      Serial.print(F("kgL=")); Serial.print(kgL,3);
      Serial.print(F(" kgR=")); Serial.print(kgR,3);
      Serial.print(F(" SUM=")); Serial.print(kgSum,3);
      Serial.print(F(" SUM*G=")); Serial.println(kgSumDisp,3);
    }
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
